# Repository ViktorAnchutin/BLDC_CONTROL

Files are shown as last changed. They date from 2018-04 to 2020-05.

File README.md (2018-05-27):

## BLDC position control project ##

### Youtube video ###

Watch the video (https://www.youtube.com/watch?v=04u3CLnnJWE)

Three techniques have been implemented:

 - Position control with sinusoidal commutation -`sinus_control_V2`
 - Position control with simplified FOC (no current sensing) - `FOC`
 - Position control with special sinusoidal commutation(vectol angle limitation) - `combined_control_V3`
  
 ### Structure ###

Essential elements:

 - STM32F4-Discovery
 - DRV8313
 - AS5048A

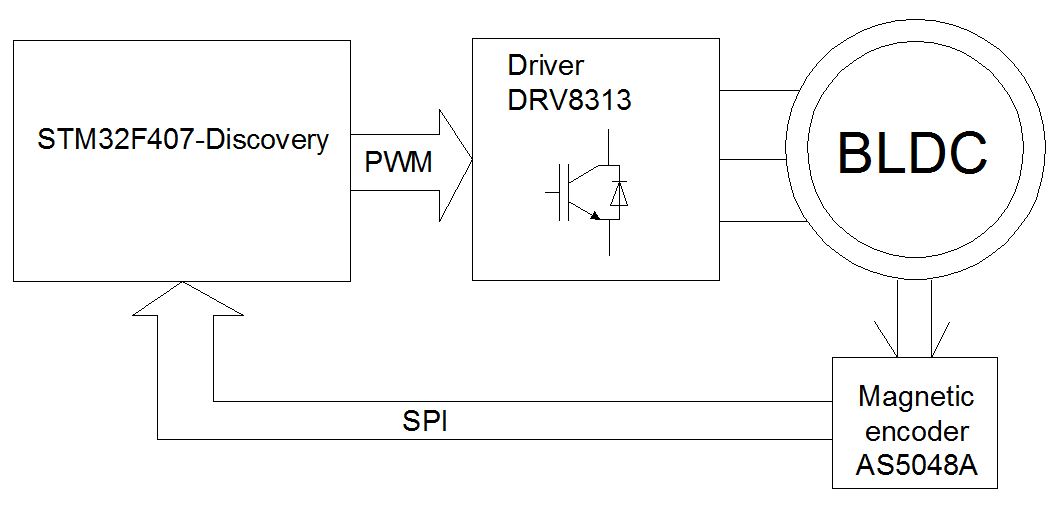
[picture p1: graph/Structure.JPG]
Alt-текст Structural scheme


### Electrical scheme ###
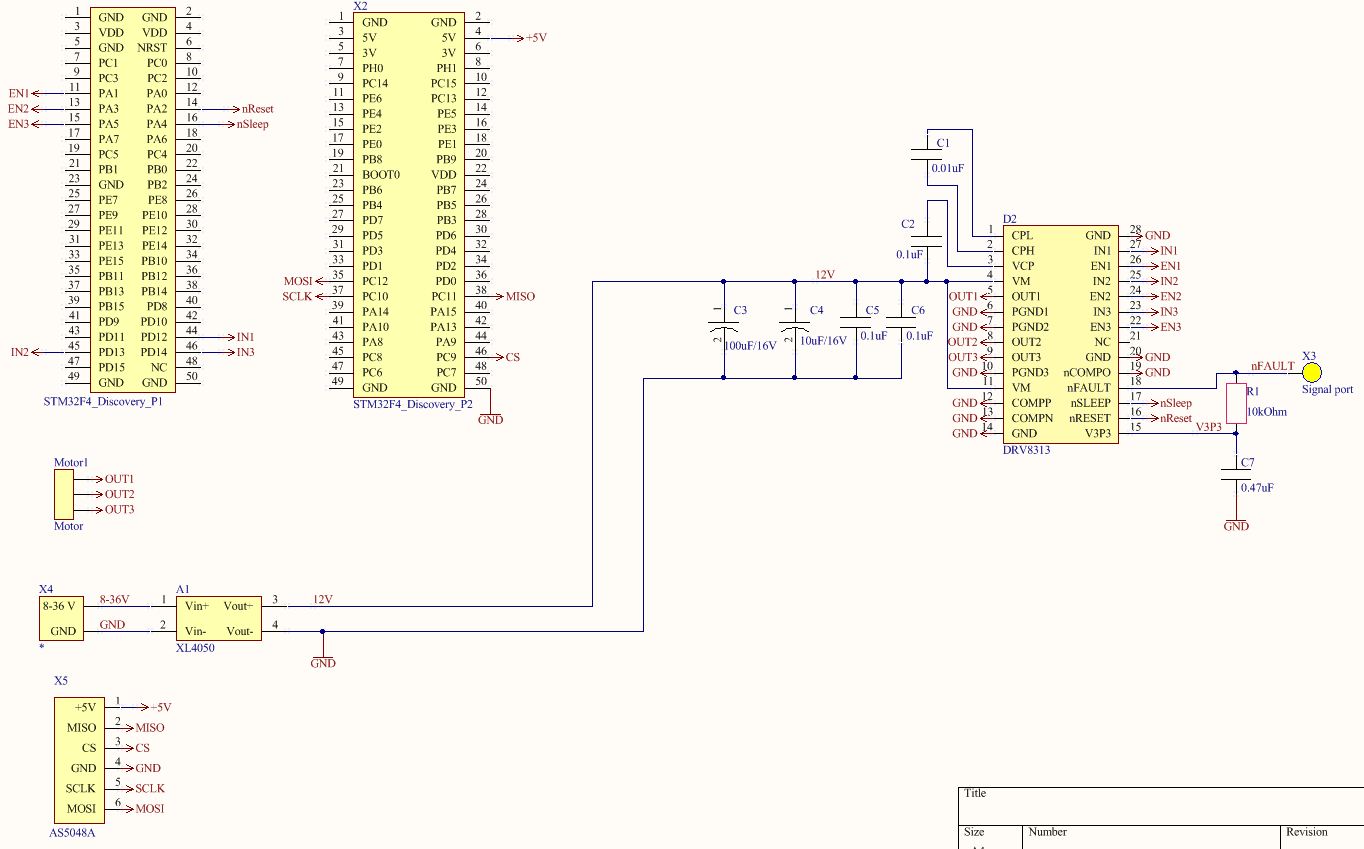
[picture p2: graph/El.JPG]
Alt-текст Electrical scheme


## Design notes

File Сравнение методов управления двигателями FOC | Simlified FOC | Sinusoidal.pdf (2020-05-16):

1.1 Исследование | методов | управления | электродвигателями | систем
стабилизации

1.1.1 Моделирование синхронного двигателя с постоянными магнитами

Уравнения статора синхронного двигателя (2) показывают, что напряжение, приложенное к обмоткам статора, расходуется на поддержание тока в обмотках статора, а также на скорость изменение магнитного потока.
[

Va
Vb
Vc

] = [R 0 0
0 R 0
0 0 R

] [ia
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
dt ]
; | (2)

Магнитный поток, формируется из собственной индуктивности ротора, а также путем добавления проекции магнитного потока ротора, формируемого постоянным магнитами.
[

ψa
ψb
ψc

] = [L 0 0
0 L 0
0 0 L

] [ia
ib
ic

] + [ψam
ψbm
ψa
] ; | (3)

В данной работе электрический угол поворота вала считается между неподвижной осью статора А и осью q вращающихся координат. Перпендикулярно оси q располагается ось d, по которой направлен вектор магнитного потока ротора.

В качестве допущений взаимные индуктивности обмоток статора не учитываются, а также предполагается, что собственная индуктивность обмоток статора не зависит от положения ротора. В этом случае индуктивности обмоток статора равны собственным индуктивностям, а также эквивалентны друг другу.

Как было сказано, вектор магнитного потока ротора направлен по оси d. На рисунке 1.3 представлена схема проекций магнитного потока ротора на стационарные оси статора.

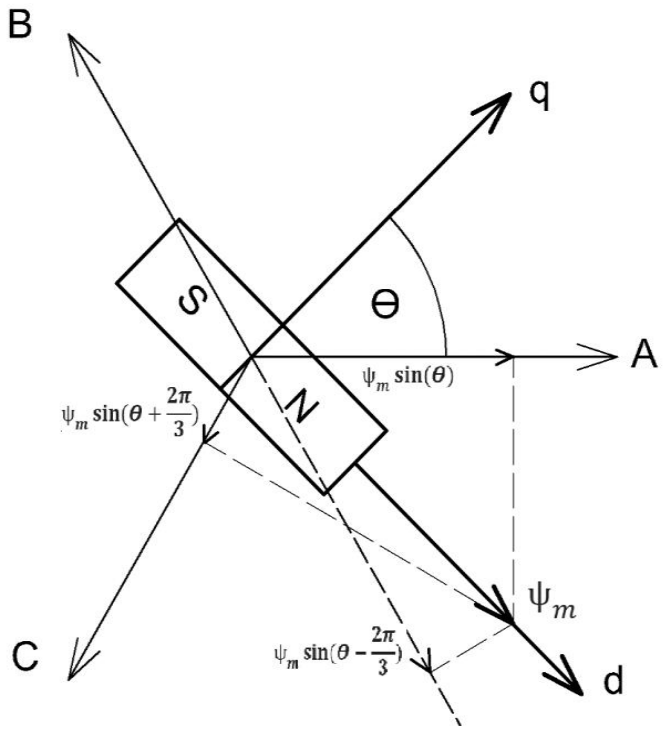
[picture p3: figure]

При отсчете электрического угла поворота ротора от оси q проекции магнитного потока ротора записываются через синус электрического угла поворота, смещенного на 120° для каждой оси.
[

ψam
ψbm
ψcm

] =

[

ψm | sin(Θ)
ψm | sin(Θ − 2π
3 | )
ψm | sin(Θ +

2π
3 )
]
; | (4)

Рисунок 1.1 -Схема проекций магнитного потока ротора

Скорость изменения составляющей магнитного потока, принадлежащей ротору, может быть представлена в виде:
[
ψ′am

ψ′bm

ψ′cm ] =

[

ψm | cos(Θ) ∙ Θ̇
ψm | cos(Θ − 2π
3 | ) ∙ Θ̇
ψm | cos(Θ +

2π
3 ) ∙ Θ̇
]

(5)

Подставив (3) и (5) в (2) получим развернутую форму уравнения напряжения статора синхронного двигателя с постоянными магнитами:

{

Va = R ∙ ia + L ∙

dia
dt + | ψm | cos(Θ) ∙ Θ̇

Vb = R ∙ ib + L ∙

dib

dt + | ψm | cos (Θ − 2π
3 | ) ∙ Θ̇

Vc = R ∙ ic + L ∙

dic

dt + | ψm | cos (Θ + 2π
3 | ) ∙ Θ̇

(6)

Из системы уравнений (7) видно, что токи статора зависят от напряжения прикладываемого к обмоткам статора, а также от формируемого противо ЭДС, зависящего от электрического угла поворота и электрической скорости вращения.

{

ia =

Va − | ψm | cos(Θ) ∙ Θ̇
R + L ∙ p

ib =

Vb − | ψm | cos (Θ − 2π
3 | ) ∙ Θ̇

R + L ∙ p

ic =

Vc − | ψm | cos (Θ + 2π
3 | ) ∙ Θ̇

R + L ∙ p

(7)

Согласно [12], а также учитывая, что в указанной статье уравнение момента выводится для двухполюсного двигателя, а также электрический угол поворота ротора считается по оси d, т.е. проекции ψm изменяются по косинусу, в то время как в данной курсовой работе электрический угол считается по оси q, получаем:

Mэл = npψm | ( ia | cos(Θ) + ib | cos (Θ − 2π
3 | ) + ic | cos (Θ +

2π
3 | ) ) ; | (8)

Математическая модель привода во вращающихся координатах имеет ряд преимуществ.

Согласно [13] матрица перехода во вращающиеся координаты записывается как:

Ks =

2
3 ∙

[

cos(Θ) | cos(Θ − 2π
3 | ) cos (Θ +

2π
3 | )
sin(Θ) | sin (Θ − 2π
3 | ) sin (Θ +

2π
3 )

1
2

1
2

1
2 | ]
; | (9)

Таким образом для получения проекций вектора напряжения статора на вращающиеся координаты ротора необходимо вектор столбец, состоящий из значений напряжений в стационарных координатах статора умножить на матрицу поворота (9).
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
cos(Θ) | cos(Θ − 2π
3 | ) cos (Θ +

2π
3 | )
sin(Θ) | sin (Θ − 2π
3 | ) sin (Θ +

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
] ; (10)

В рассматриваемой модели предполагается, что сопротивления обмоток статора равны, а так как сумма токов статора равна нулю, то третий компонент вектора V0 равен нулю и не представляет интереса для дальнейшего моделирования.

Матрица обратного преобразования выглядит следующим образом:

(Ks)⁻¹ =
[
cos(Θ) | sin(Θ) | 1
cos(Θ − 2π
3 | ) sin (Θ − 2π
3 | ) 1

cos (Θ +

2π
3 | ) | sin (Θ +

2π
3 | ) 1]
; | (11)

Соответственно обратный переход от вращающихся к стационарным координатам имеет вид:
[

Va
Vb
Vc

] =

[

cos(Θ) | sin(Θ) | 1
cos(Θ − 2π
3 | ) sin (Θ − 2π
3 | ) 1

cos (Θ +

2π
3 | ) | sin (Θ +

2π
3 ) 1]

[
Vq
Vd
V0
] ; | (12)

Систему уравнений напряжений статора можно представить в векторной форме, выразив через векторы во вращающихся координатах:

(Ks)⁻¹ ∙ Vqd0 = R ∙ (Ks)⁻¹ ∙ iqd0 +

d
dt ( (Ks)⁻¹ ∙ ψqd0 | ) | (13)

Учитывая, что матрица преобразования координат зависит от электрического угла поворота, скорость изменения магнитного потока в уравнении (13) можно представить в следующем виде:

(Ks)⁻¹ ∙

dψqd0
dt +

d(Ks)⁻¹
dt | ∙ ψqd0 | =

= (Ks)⁻¹ ∙

dψqd0
dt +

d(Ks)⁻¹
dΘ ∙

dΘ
dt ∙ ψqd0

(14)

Выразим производную матрицы преобразования координат по электрическому углу поворота следующим образом:

d(Ks)⁻¹
dΘ =
[
−sin(Θ) | cos(Θ) | 0
−sin(Θ − 2π
3 | ) cos (Θ − 2π
3 | ) 0

−sin (Θ +

2π
3 | ) | cos (Θ +

2π
3 | ) 0]
= | (15)

= (Ks)⁻¹ ∙ [

0 1 0
−1 0 0
0 0 0

] ;

Теперь подставляя уравнения (15) и (14) в (13), а также сократив уравнения на (Ks)⁻1 получаем:

Vqd0 = R ∙ iqd0 +

dψqd0

dt + [ ⁰ 1 0
−1 0 0
0 0 0

] [

Θ̇ ∙ ψq
Θ̇ ∙ ψd
Θ̇ ∙ ψ0
] ; | (16)

Так как взаимные индуктивности обмоток статора не учитываются, а также предполагается, что собственная индуктивность обмоток статора не зависит от положения ротора. Тогда согласно уравнениям 3.61 и 3.62 из [14]:

Lq = Ld = L | (17)

Согласно уравнениям 5.2 из [15] потокосцепления по осям d и q могут быть выражены как:
{

ψq = L ∙ iq
ψd = L ∙ id + ψm

(18)

Таким образом уравнения напряжений статора во вращающихся координатах можно записать следующим образом:
{
Vq = R ∙ iq + L ∙

diq
dt + (L ∙ id + ψm) ∙ Θ̇

Vd = R ∙ id + L ∙

did
dt + (L ∙ iq) ∙ Θ̇

(19)

Получив уравнения токов можно заметить, что они зависят от напряжения, прикладываемого по осям dq, а также от величины проекции противо ЭДС на вращающиеся координаты ротора, причем противо ЭДС по оси d не зависит от величины магнитного потока ротора, так как он направлен перпендикулярно оси q:

{

iq =

Vq − ω ∙ (L ∙ id + ψm)
L ∙ p + R

id =

Vd + ω ∙ (L ∙ iq)
L ∙ p + R

(20)

Здесь p – оператор дифференцирования, ω - скорость электрических оборотов ротора.

Согласно [13] уравнение момента в переменных d-q может быть представлено в виде:

M =

3
2 ∙ np ∙ (ψd | ∙ iq − ψq | ∙ id) ; | (21)

Преобразуя данное выражение, после подстановки выражений потокосцепления, получим:

M =

3
2 ∙ np ∙ (id ∙ iq ∙ (Ld − Lq) + ψm | ∙ iq) ; | (22)

Учитывая, тот факт, что индуктивность по осям d-q эквивалентна, получаем уравнение момента:

M =

3
2 ∙ np ∙ ψm | ∙ iq ; | (23)

1.1.2 Методы позиционирования синхронного двигателя в задаче стабилизации

Практически все методы позиционирования основываются на теоретической модели двигателя. Эта модель представляет собой систему координат статора, состоящую из трех осей – фаз А, B и C, повернутых друг относительно друга на 120 градусов.

Система координат, связанная с ротором, состоит из двух перпендикулярных осей координат. По оси d направлен магнитный поток ротора.

Задать ориентацию магнитного поя статора можно несколькими способами. Первый способ используется при управлении скоростью двигателя. Он позволяет предусматривает 6 положений вектора тока статора на один электрический оборот. Эти положения задаются определенной комбинацией состояний ключей инвертора. Ниже представлена диаграмма напряжений для формирования данных векторов, где A, B, C – средние точки полумостов инвертора. В формировании вектора учувствуют две фазы, которые замыкаются друг на друга, путем включения верхнего транзистора одного полумоста и включением нижнего транзистора другого полумоста.

Таким образом, формируется вращающееся поле статора со скоростью вращения, равной скорости вращения вектора напряжения. Однако для задач позиционирования данный способ не подходит, так как присутствует слишком большая дискретность по положению вектора напряжения, вследствие чего происходят скачки момента, на маленькой скорости перемещение происходит рывками, а точность принятия положения ограничена 60 электрическими градусами. Поэтому необходимо формировать непрерывно вращающийся вектор, который мог бы занимать любое положение.

1.1.2.1 Скалярный метод позиционирования

Данный подход является самым простым методом управления положением и позволяет решать задачи позиционирования так как обеспечивает непрерывное вращение вектора с неограниченным количеством положений, а также не требует измерения положения ротора.

Это достигается путем подачи синусоидального напряжения со смещением между фазами в 120 электрических градусов.

На рисунке 1.4 совмещены диаграммы напряжений блочной коммутации, описанной выше, и скалярного метода, использующего синусоидальную коммутацию.

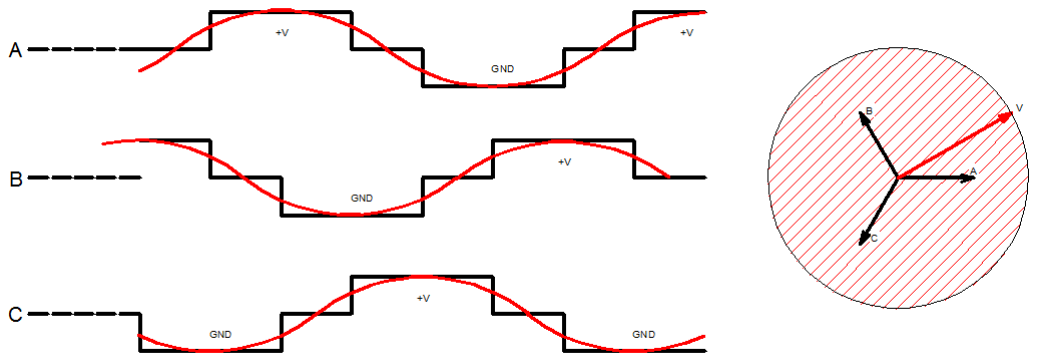
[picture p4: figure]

Формирование вектора напряжения, а следовательно, и ориентация поля, происходит путем задания напряжений в фазах двигателя, вычисленных через функции косинусов, сдвинутых друг относительно друга на 120 градусов. Это позволяет иметь синусоидальные токи в фазах, а значит и непрерывное вращение магнитного поля статора, это показано штриховкой на рисунке 1.4.

Задания напряжений в фазах статора формируются следующим образом:

{

VA = V ∙ cos(Θe)
VB = V ∙ cos (Θe − 2π
3 )

VC = V ∙ cos (Θe +

2π
3 )
; | (24)

Рисунок 1.2 – Диаграммы напряжений при разных способах коммутации

Коммутация обмоток происходит синусоидальным способом. При данном способе напряжения средних точке инвертора вычисляются следующим образом:

{

Vinv1 = VA +

Vпит
2

Vinv2 = VB +

Vпит
2

Vinv3 = VC +

Vпит
2
; | (25)

Амплитуда вектора является постоянной и задается на этапе инициализации.

Угол вектора напряжения в скалярном управлении можно отсчитывать от любого начального положения.

Вращение поля осуществляется изменением значения угла вектора напряжения. Таким образом позиционирование осуществляется путем контролирования и изменения значения угла поворота вектора напряжения.

При вращении вектора напряжения статора магнитное поле ротора следует за формируемым магнитным полем статора. При наличии сигнала рассогласования он поступает в регулятор положения, который вырабатывает величину прибавляемую к текущему значению вектора и тем самым стремится вращать поле статора в направлении уменьшения ошибки позиционирования.

Таким образом, управляя величиной изменения угла вектора напряжения происходит управление скоростью его вращения. Поэтому с увеличением значения ошибки будет увеличиваться шаг инкрементирования положения вектора напряжения, а следовательно, и скорости вращения поля статора.

Структурная схема системы скалярного управления положением представлена на рисунке 1.5. Регулятор производит операцию регулирования шага изменения угла вектора, который преобразуется в фазовые напряжения.

Параметры регулятора подбираются в зависимости от частоты цикла работы системы.

Как видно задание необходимого угла вектора напряжения происходит путем дискретного интегрирования шага изменения.

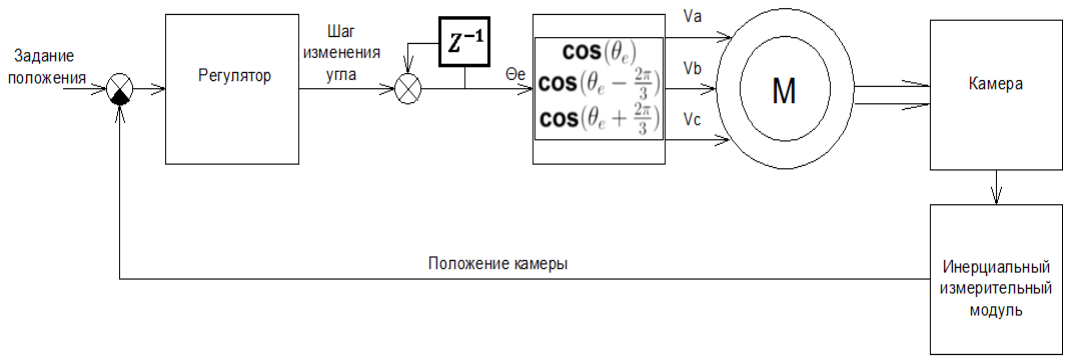
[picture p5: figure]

Плюсами данного метода являются простота реализации и дешевизна ввиду отсутствия необходимости измерения положения вала.

К минусам данного метода можно отнести то, что вектор напряжения присутствует постоянно, меняется лишь его угол, а значит происходит большое потребление энергии, вследствие чего моторы могут перегреваться.

Также стоит отметить, что при резком ускорении или превышении допустимой нагрузке системы происходит рассинхронизация полей ротора и статора, что приводит систему в неработоспособное состояние до перезагрузки алгоритма управления.

Рисунок 1.3 – Функциональная схема системы скалярного управления

Отсутствие измерения положения ротора не позволяет точно решать задачу обратной кинематики, а значит и проектировать точные системы стабилизации на основе многоосевых модулей при больших углах качки.

Также одним из главных недостатков скалярного управления с точки зрения стабилизации это то, что этот метод не позволяет использовать физические преимущества строения систем стабилизации, а именно не позволяет объекту стабилизации использовать собственную массу ц целях стабилизации.

1.1.2.2 Система векторного управления

Уравнения синхронного двигателя во вращающихся координатах имеют нелинейные зависимости от угла поворота ротора. В частности, как видно из уравнений (6), значения противо ЭДС обмоток статора зависят от косинусов электрического угла поворота ротора. С целью избавления от нелинейных зависимостей от угла поворота вала переходят во вращающиеся координаты ротора. Данный переход заменяет три уравнения в стационарных координатах, имеющих тригонометрические зависимости от угла поворота вала, двумя во вращающихся ортогональных координатах ротора.

Уравнение (23) показывает, что момент, создаваемый двигателем, зависит только от тока по оси q. Из уравнений (20) видно, что ток по оси q зависит не только от напряжения по оси q но и от величины тока по оси d, следовательно можно добиться линейной зависимости момента от входного напряжения, только путем поддержания величины тока по оси d постоянной. Из уравнений
(20) видно, что в целях достижения максимальной эффективности следует поддерживать ток по оси d равным нулю. Стоит отметить, что в этом случае вектор тока статора будет перпендикулярен вектору магнитного потока ротора, это показано на рисунке 1.6.

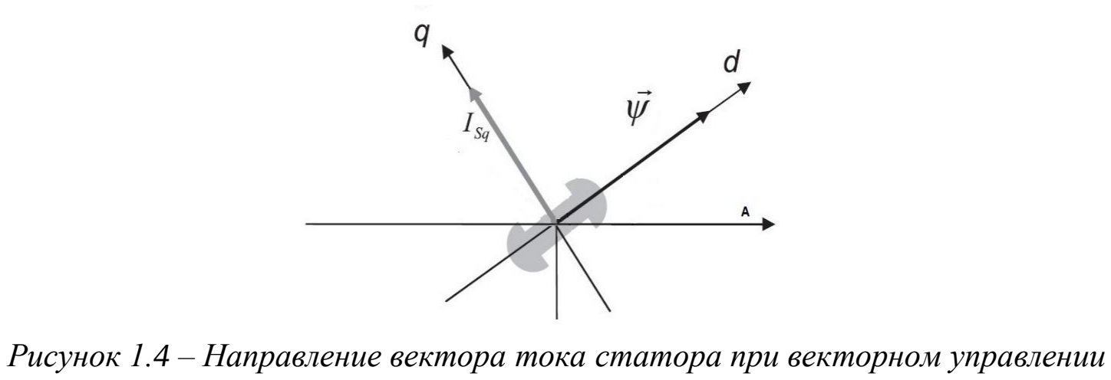
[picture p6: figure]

Для поддержания тока статора по оси d равным нулю используется регулятор тока, который формирует соответствующее значение напряжения по оси d. Из (12) следует, что задания напряжений фаз статора формируются следующим образом

{

Va = cos(Θ) Vq + sin(Θ) Vd Vb = cos (Θ − 2π

3 ) Vq + sin (Θ − 2π
3 ) Vd

Vc = cos (Θ +

2π
3 ) Vq + sin (Θ +

2π
3 ) Vd
; | (26)

Применение векторного управления в задаче стабилизации целесообразно в устройствах многоосевой стабилизации в условиях качки с большой амплитудой, так как наличие датчика положения вала позволяет применять обратную задачу кинематики в динамике.

Система векторного управления позволяет проектировать систему стабилизации используя методы линейной теории автоматического управления.

Как было сказано, что необходимым условием обеспечения линейной зависимости между входным напряжением и моментом, создаваемым

Рисунок 1.4 – Направление вектора тока статора при векторном управлении синхронным двигателем, является поддержание тока статора, рассматриваемого во вращающихся координатах, по оси d равным нулю. В таком случае система управления должна иметь два канала регулирования.

Основной канал регулирования проектируется в предположении, что зависимость между входным напряжением по оси q и выходным моментом является линейной. В этом случае в качестве объекта управления рассматривается линейная модель эквивалентного двигателя. Это позволяет использовать законы линейной теории автоматического управления при проектировании корректирующего устройства основного канала регулирования. Таким образом, основная задача данного канала управления в проектируемой системе – это регулирование положения вала двигателя в соответствие с заданием.

Вспомогательный канал регулирования поддерживает ток по оси d равным нулю, тем самым выполняя необходимое условие для корректной работы основного канала управления.

Как видно из уравнения (20) токи по оси q и оси d имеют взаимовлияния. Так, противо ЭДС по оси d формируется током по оси q и электрической скоростью вращения вала. Следует отметить, что противо ЭДС является причиной возникновения тока по оси d, при нулевом задании напряжения по оси
d. Противо ЭДС по оси q зависит не только от магнитного потока ротора и скорости его вращения, но также от тока по оси d.

Поэтому необходимо ввести компенсацию противо ЭДС, которая будет устранять взаимовлияния каналов управления, а также поддерживать ток по оси d равным нулю при задании нулевого напряжения по оси d.

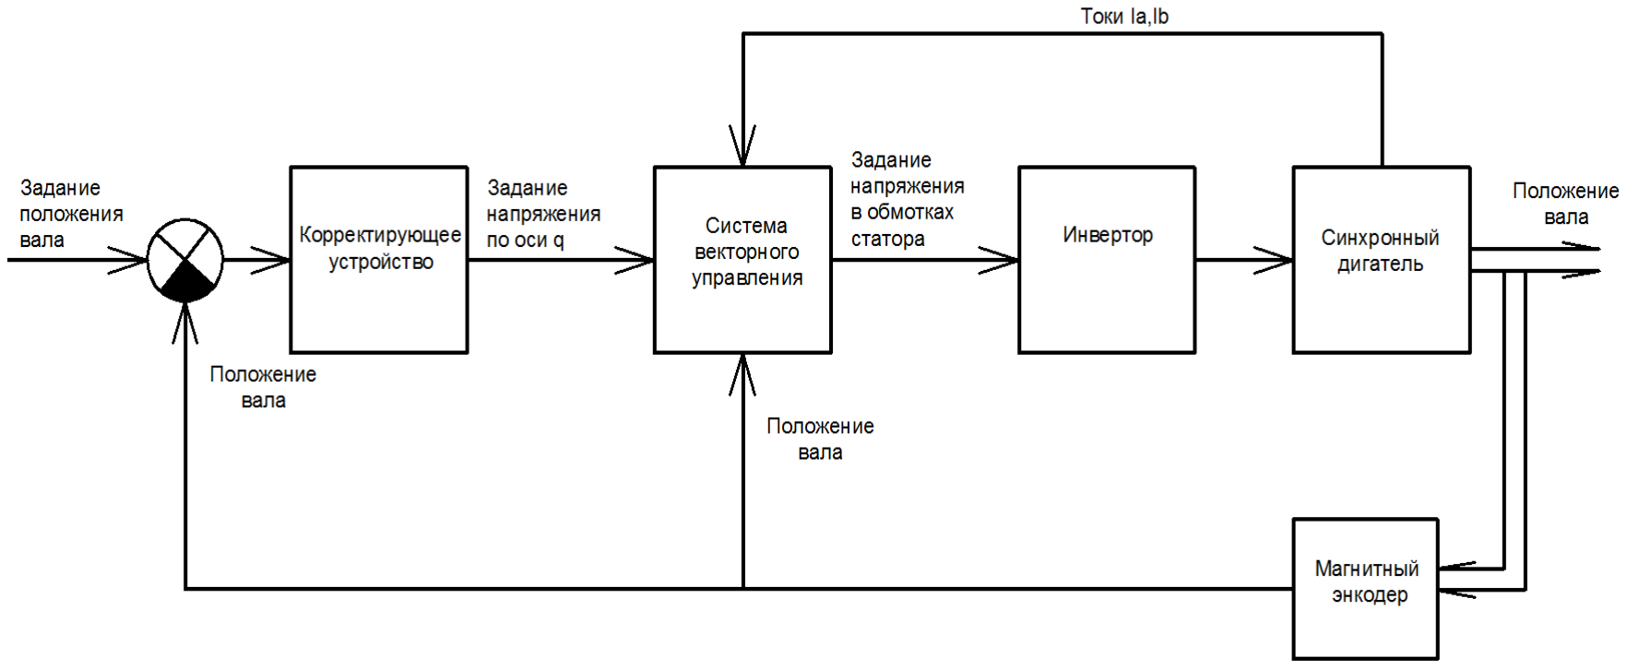
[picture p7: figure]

Принципиальная схема системы управления положением вала на рисунке 1.7.

Таким образом, величина рассогласования поступает в корректирующее устройство, которое рассчитывает напряжение, которое необходимо сформировать по оси q, в предположении, что ток по оси d равен нулю, а, следовательно, система линейна. Данное условие выполняет система векторного управления, которая на основании положения вала и полученного задания напряжения по оси q рассчитывает необходимое задание напряжения для фаз двигателя, таким образом, чтобы вектор тока статора был направлен перпендикулярно вектору магнитного потока ротора.

С точки зрения систем стабилизации векторное управление имеет ряд преимуществ по сравнению со скалярным управлением. Во-первых, векторное управление позволяет ротору свободно вращаться при отсутствии ошибки стабилизации, тем самым позволяя камере использовать свою массу для самостабилизации. Во-вторых, векторное управление не потребляет энергию в статическом состоянии, что позволяет продлить время использования автономных источников питания.

Также, было отмечено, что система векторного управления позволяет привести модель синхронного двигателя к линейной, а значит использовать

Рисунок 1.5 – Функциональная схема системы управления двигателем методы линейной теории автоматического управления в целях расчета корректирующего устройства.

К недостаткам системы векторного управления можно отнести высокую сложность реализации, а также необходимость знания физических параметров двигателя с целью расчета корректирующего устройства.

1.1.2.3 Система векторного управления без измерения токов статора

Векторы тока и напряжения имеют следующую зависимость:

{

iq =

Vq − ω ∙ (L ∙ id + ψm)
L ∙ p + R

id =

Vd + ω ∙ (L ∙ iq)
L ∙ p + R

(27)

Отсюда видно, что вектор тока отличается от вектора напряжения из-за наличия инерционности вносимой электрической постоянной времени, а также их разница возрастает при увеличении скорости вращения ротора, то есть при увеличении значения противо ЭДС.

Предполагается, что в системе стабилизации двигателю не приходится отрабатывать скорости, на которых противо ЭДС значительно влияет на разницу между векторами напряжения и тока.

Моделирование работы синхронного двигателя с постоянными магнитами показало, что при векторном управлении по вектору напряжения ток по оси d в режиме стабилизации незначителен и не привносит существенной ошибки в работу системы по сравнению с методом полного векторного управления. Структурная схема упрощенного векторного управления представлена на рисунке 1.8.

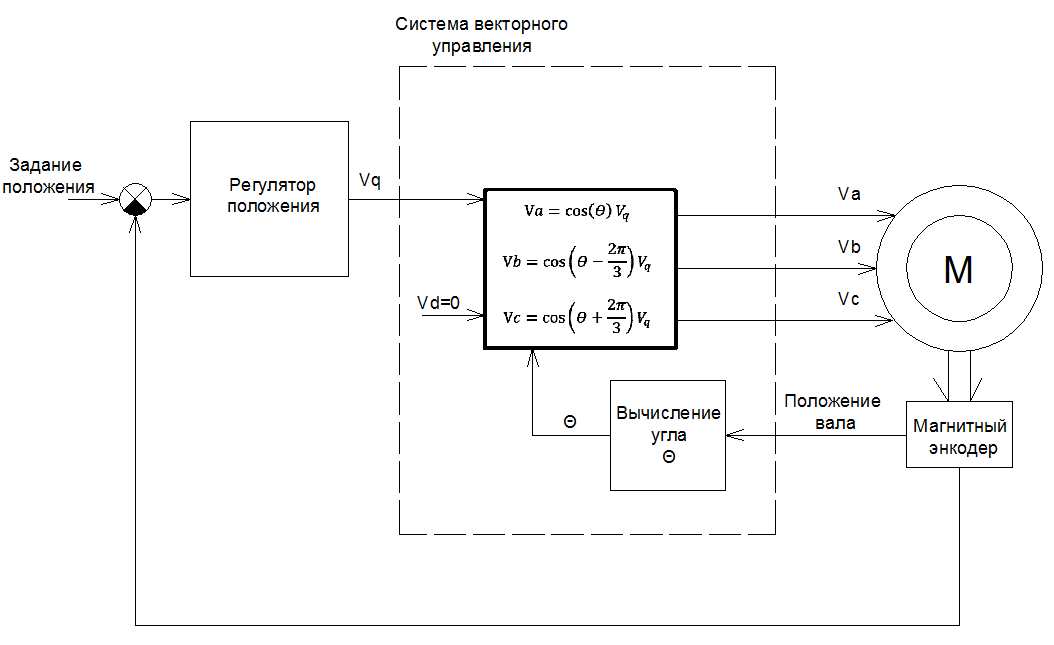
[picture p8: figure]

Рисунок 1. 8 – Функциональная схема системы управления двигателем

При данном способе напряжение по оси d прикладывается равным нулю, следовательно, фазные напряжения могут быть рассчитаны по формулам:

{

Va = cos(Θ) Vq
Vb = cos (Θ − 2π
3 ) Vq

Vc = cos (Θ +

2π
3 ) Vq
; | (28)

Таким образом упрощенное векторное управление позволяет управлять синхронным двигателем с постоянными магнитами в задачах стабилизации и использовать линейные законы управления при условии, что двигателю не приходится отрабатывать скоростей, при которых генерируемое проитво ЭДС вносило бы значительную разницу между векторами тока и напряжения.

1.1.3 Выбор способа управления двигателем

На основе проведенного анализа методов управления положением синхронного двигателя, а также учитывая специфику работы систем стабилизации было принято решение использовать метод векторного управления без измерения токов для управления приводами стабилизации, в предположении, что скорости обкатки приводов не создадут значительной разницы между векторами напряжения и тока.
Данный метод обладает всеми преимуществами векторного управления, а также упрощает его реализацию ввиду того, что не производится измерение токов.

Векторное управление позволит рассчитать корректирующие устройства для приводов стабилизации, используя метод частотного синтеза.

1.1.4 Приведение модели синхронного двигателя к линейной

Как было показано, для расчета корректирующего устройства основного канала регулирования необходимо получить линейную модель эквивалентного двигателя. Это достигается путем приравнивая тока по оси d к нулю:

{

iq =

Vq − ω ∙ ψm
L ∙ p + R

M =

3
2 ∙ np ∙ ψm ∙ iq

(29)

Таким образом, можно отметить, что полученные уравнения соответствуют уравнения модели эквивалентного двигателя постоянного тока.

Подставим уравнения линейной модели (29) в уравнение динамики вращательного движения:

p ∙ ωm ∙ J = 3
2 ∙ np ∙ ψm ∙

Vq − ωm ∙ np ∙ ψm
L ∙ p + R | ; | (30)

Здесь ωm – механическая скорость вращения ротора, np - количество пар полюсов, p – оператор дифференцирования.

Примем следующие обозначения:
{
np ∙ ψm | = k2
np ∙ ψm | ∙

3
2 = k1

(31)

Выразим зависимость скорости вращения двигателя от входного напряжения:

ωm = (Vq − ωm ∙ k2) ∙ [ 1
(L ∙ p + R)
- k1
| J ∙ p];
(32)

ωm ( k2 ∙ k1
(L ∙ p + R) ∙ J ∙ p
+ 1) = Vq ∙ | k1 (L ∙ p + R) ∙ J ∙ p
;
(33)

ωm
Vq
= | k1 (L ∙ p + R) ∙ J ∙ p + k2 ∙ k1
=

1
k2
(L ∙ p + R) ∙ J ∙ p
k2 ∙ k1

+ 1

=

=

1
k2
(L ∙ p) ∙ J ∙ p
k2 ∙ k1

+

R ∙ J ∙ p
k2 ∙ k1

+ 1

=

=

1
k2
R ∙ J
k2 ∙ k1

∙

L

R ∙ p² + R ∙ J k2 ∙ k1
- p + 1

;

(34)

Примем следующие обозначения для механической и электрической постоянных времени:

{

Tm = R ∙ J k2 ∙ k1

Te =

L
R

(35)

В силу малости электрической постоянной времени зависимость скорости от входного напряжения можно представить в виде:

ωm
Vq

=

1
k2
(Tm ∙ p + 1) ∙ (Te ∙ p + 1) ; | (36)

Таким образом передаточная функция, выражающая связь между входным напряжением и углом поворота вала имеет вид:

W(p)дв =

1
k2
(Tm ∙ p + 1) ∙ (Te ∙ p + 1) ∙ p

(37)

1.3.5 Выводы

Плюсами скалярного метода являются простота реализации и дешевизна ввиду отсутствия необходимости измерения положения вала.

К минусам данного метода можно отнести то, что вектор напряжения присутствует постоянно, меняется лишь его угол, а значит происходит большое потребление энергии, вследствие чего моторы могут перегреваться.

Также стоит отметить, что при резком ускорении или превышении допустимой нагрузке системы происходит рассинхронизация полей ротора и статора, что приводит систему в неработоспособное состояние до перезагрузки алгоритма управления.

Отсутствие измерения положения ротора не позволяет точно решать задачу обратной кинематики, а значит и проектировать точные системы стабилизации на основе многоосевых модулей при больших углах качки.

Также одним из главных недостатков скалярного управления с точки зрения стабилизации это то, что этот метод не позволяет использовать физические преимущества строения систем стабилизации, а именно не позволяет объекту стабилизации использовать собственную массу ц целях стабилизации.

С точки зрения систем стабилизации векторное управление имеет ряд преимуществ по сравнению со скалярным управлением.

Во-первых, векторное управление позволяет ротору свободно вращаться при отсутствии ошибки стабилизации, тем самым позволяя камере использовать свою массу для самостабилизации.

Во-вторых, векторное управление не потребляет энергию в статическом состоянии, что позволяет продлить время использования автономных источников питания.

Также, было отмечено, что система векторного управления позволяет привести модель синхронного двигателя к линейной, а значит использовать методы линейной теории автоматического управления в целях расчета корректирующего устройства.

К недостаткам системы векторного управления можно отнести высокую сложность реализации, а также необходимость знания физических параметров двигателя с целью расчета корректирующего устройства.

В дальнейшем, при проектировании мехатронного стабилизатора, применяется система векторного управления двигателем. Для такого типа управления была получена передаточная функция двигателя.

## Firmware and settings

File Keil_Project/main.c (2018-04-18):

#include "stm32f4xx.h" 
#include "as5048.h"
#include "stm32f4xx_gpio.h"
#include "stm32f4xx_rcc.h"
#include "stm32f4xx_spi.h"
#include "mylib.h"
#include "init.h"
#include "motor.h"
#include <stdio.h>


uint8_t mode;
float angle, angle_error, angle_test, angle1, angle_error_mem_in1, angle_error_mem_in2, angle_error_mem_in3, angle_error_mem_out1, angle_error_mem_out2, angle_error_mem_out3;
float des_val,des_val1;
uint32_t t1, t2, t3, t4, dt1, dt22, p, timex, t1_IMU, t2_IMU, dt_IMU;

float voltage, current;

float sin_x, cos_x, tv_g, t_g, t_d;

uint8_t ADC_started;

// moving average filter variables


uint8_t filled_ADC;
	uint16_t i_ADC; // counter for filling in
	float data_ADC;
	float arr_ADC[window_ADC],  angle_average, a_i_ADC,  des_val_raw; // variables for first order moving average
	uint16_t k_ADC; // counter
	float ADC_average;
	uint8_t flag_ADC;
  uint32_t sum_ADC;
	
	
	//moving average Roll
	
	uint8_t filled_Roll;
	uint32_t i_Roll; // counter for filling in
	float data_Roll;
	uint32_t arr_Roll[window_Roll],  Roll_average, a_i_Roll; // variables for first order moving average
	uint32_t k_Roll; // counter
	
	uint8_t flag_Roll;
  uint32_t sum_Roll;
	
	
	
	
	
	
	
	


uint16_t USART_count;
uint8_t IMU_data_ready;

uint16_t IMU_Recieve_Buf[11];
uint8_t IMU_count;
uint16_t USART_test_rec;
uint8_t IMU_data;

float Pitch, Roll, Yaw;
float Roll_raw, roll_sine, roll_cos, Roll_raw_test, roll_sine_test, roll_cos_test, Roll_test, Roll_cor;

 moving_average_type ADC_filter;
 
 
 uint8_t first_ini;
 
 
 
 
 

int main(void)
	
{
	
	
	
	USART_2_init();
	SPI3_ini();
	user_button_init();
	
	
	TIM5_ini(); // Delay timer
		
	TIM4_ini(); // PWM timer	
	
	PWM_INx_init();
	ENx_init();
	ADC_initt();
	Set_nRes_nSleep();
	Set_ENx();
	FOC_InitPosition();
	
	des_val = 36; ///////////////


	while(1)
	{
		
		
		if(!ADC_filter.filled)
		{
			while(!ADC_filter.filled); // wait for adc filter ready
		} 
		
		
			
			t1 = TIM5->CNT;
		
		
	

		
		
		
	angle = CQ_average_angle();
		
  des_val = ADC_average*360/4095;
  
	angle_error = des_val - angle;
		
	
		
	
	if(mode==0)	FOC(angle, angle_error, 1.1,   0,  0.01,  dt1)	;		
 
	if(mode==1) sinus_control_V2(angle_error, 6, 0.001, 0.05);
		
	if(mode==2)combined_control_V3(angle, angle_error, 6, 0.001, 0.05);
		
			t2 = TIM5->CNT;
			dt1 = t2 - t1;
	

		
	
	}
}




void EXTI0_IRQHandler(void) {
	
	if (EXTI_GetITStatus(EXTI_Line0) != RESET) {		
			
			EXTI_ClearITPendingBit(EXTI_Line0);
		 NVIC_DisableIRQ(EXTI0_IRQn);
		
		mode++;
			if(mode>2) mode=0;
		
		NVIC_EnableIRQ(EXTI0_IRQn);
		
	}
	
}




void ADC_IRQHandler()
	{
		if(ADC_GetITStatus(ADC1,ADC_IT_EOC) !=RESET)
		{
			
			
			ADC_ClearITPendingBit(ADC1, ADC_IT_EOC);
			
			ADC_average =  moving_average(&ADC_filter, (float)ADC_GetConversionValue(ADC1), 2000);
						
			ADC_RegularChannelConfig(ADC1, ADC_Channel_9, 1, ADC_SampleTime_480Cycles);
	    
			ADC_SoftwareStartConv(ADC1);
									
		}
		
	}  
	
	
	
	
	void USART2_IRQHandler()
{
	if(USART_GetITStatus(USART2, USART_IT_TXE)==SET)
	{
		USART_ClearITPendingBit(USART2, USART_IT_TXE);
		
		
	}
	
	if(USART_GetITStatus(USART2, USART_IT_RXNE)==SET)
	{
		USART_ClearITPendingBit(USART2, USART_IT_RXNE);
	//	USART_test_rec = (uint8_t)USART_ReceiveData(USART2);
		
		USART_test_rec = USART_ReceiveData(USART2);
		
		if(IMU_data==0)
		{
			if(USART_test_rec==0x55)
			{
				IMU_data=1;
			}
		}
		
		else if(IMU_data==1)
		{
			if(USART_test_rec==0x53)
			{
				IMU_data = 2;
			}
			else
			{
				IMU_data=0;
			}
		}
		
		else if (IMU_data==2)
		{
			if(IMU_count<6)
			{
			IMU_Recieve_Buf[IMU_count]=USART_test_rec;
			IMU_count++;
			}
			else
			{
				IMU_data_ready=1;
				IMU_count=0;
				IMU_data=0;
			}
		}
		
		
	}
	
	
}
	

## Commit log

2018-04-08 Добавил файлы
    [Motor_PCB.PrjPcb, PCB1.PcbDoc, PcbLib1.PcbLib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]
2018-04-09 Сделал новый алгоритм
    Новый алгоритм не позволяет пропускать шаги при синусоидальной коммутации
2018-04-12 Закомментировал юарт и IMU
2018-04-14 добавил переклчение режимов по кнопке
2018-04-15 + фильтр структура
2018-04-18 + IMU sys test
